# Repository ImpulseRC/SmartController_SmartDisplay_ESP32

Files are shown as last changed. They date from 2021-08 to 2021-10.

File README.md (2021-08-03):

# [ SmartController & SmartDisplay ]
⚠️ **Warning : this is work in progress. I decline all responsability about using informations from this project** ⚠️

To contribute and help this project :

 

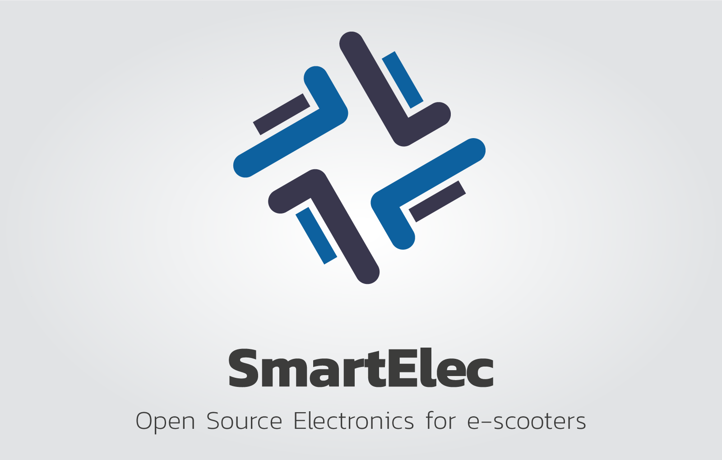
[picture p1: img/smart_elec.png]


## What is SmartController ?
It's a combo of electronic and smartphone application. It extend all features from original Minimotors EYE LCD and Minimotors controller, but it can also interface Zero, Apollo, Vsett, VESC adnd Kelly controllers.
The electronic board will interract with most of the e-scooter electronic when you plug it.
You simply place the little box inside the deck and connect it to the controller (and other electric parts if you want more features)

## What is SmartDisplay ?
It is an extension of the SmartController to completly replace the standard display of the escooter.
It mainly uses the same hardware/software.
For hardware, you only need to add a small extension board with the correct FPC connector... and of course, the LCD screen.

Render_night

## Requirements
- An e-scooter with any supported controllers (single or dual)
- An power supply between 36V and 100V... (possible with external DC-DC providing 5V if needed)
- If you want to use progressive brake feature, you must ensure no more than 60V pass in the brake handle (issue noted only for Kaabo)
- The electronics (ESP32 Dev KitC V4 + SmartController shield + JST SM/PH connectors + SmartDisplay shield if you want to connect the LCD display)
- Some electronic skills

## Features
| **Features** | **SmartController** | **SmartDisplay** | **Note** |
|:---|:---:|:---:|:---|
| Waterproof display with 3.5" screen | | ✅ | Need a custom lcd enclosure with handlebar bracket. |
| Progressive electric brake | ✅ | ✅ | |
| Temporary disable electric brake on high voltage | ✅ | ✅ | |
| Bluetooth android application with dashboard and settings | ✅ | ✅ | |
| Bluetooth and Wifi security integrated | ✅ | ✅ | BLE Encryption, Wifi WPA, HTTPS OTA |
| Wifi web application with dashboard and settings | ✅ | ✅ | |
| Intelligent battery autonomy computing with LG MJ1 cell reference | ✅ | ✅ | |
| Anti-theft with bluetooth proximity and manual locking | ✅ | ✅ | Up to 2 Bluetooth devices can be registered and scanned |
| Fast mode, acceleration, eco switches with smartphone | ✅ | ✅ | |
| Fast mode, acceleration, eco switches with custom hardware remote | ✅ | ✅ | Need a custom buttons enclosure with handlebar bracket. |
| Automatic shutdown after inactivity | ✅ | ✅ | |
| Custom acceleration curves | ✅ | ✅ | |
| Configurable speed limiter with fast on/off | ✅ | ✅ | |
| Multiple monitoring option like temperature, humidity, current/power | ✅ | ✅ | With SmartDisplay, it needs external sensors. |
| Push to start mode (PAS) | ✅ | ✅ | |
| Compatibility with Dualtron, Speedway, Futecher, Zero, Vsett, VESCs | ✅ | ✅ | VSett needs confirmation but it seems to be the same as Zero. Dual VESC needs work. |
| Over the air update with wifi connection | ✅ | ✅ | |
| Data logging on smartphone | ✅ | ✅ | |

## What can be done ?
I suggest you to have a look at all planed/added features in the image below.
There is almost no limit in custom features.
The controller power cannot exceed the nominal power, but with a shunt, you can increase the acceleration and still have a current control loop to limit the current by software (and avoid burning the controller).

Most settings will be configurable by the smartphone, and additionnal hardware buttons will allow you to control specific features.

Some examples : 
- It can lock the escooter with bluetooth proximity (with a beacon, the smartphone or any bluetooth device). When locked, the power is so reduced that nobody can ride it is you aren't close enouth. You can also manually lock the scooter with the Smartphone.

- You find the acceleration trigger to agressive at low speed ? you can change the acceleration curve for smooth trigger at low speed, and still have the beast once you push the trigger harder

- You want a mode for some weather conditions like 'rainy' with less torque ? no problem. Use fast settings access on the application dashboard or configuration hardware buttons.

- You feel the electric brake too strong at full power ? The progressive electric braking adjust the brake power with digital, or better, analog brake lever pressure sensor in real time.

- You can to limit speed to legal limits at startup ? Simply enable the option, and the speed limit can be removed with a brake pressure at startup or the smartphone.

- You want to control all settings for the Smartphone ? Use the Android native application or you can connect any device to the SmartElec in Wifi

- You want to know if there is not issue inside you escooter deck ? Temperature and humidity sensors will tell you is water entered inside the deck or if the ESC/battery is overheating.

**>>> [Check all detailed features here](/documents/FEATURES.md) <<<**

## Board assembly (v1.4.2)
Ass1

Ass2

Ass3

## Wrapping & Size
Current PCB size : 6.5cm (7cm with display connector) x 3.0cm x 1.5cm

Idea

## Electronic
### Compatibility
The software is designed for [ESP32 Dev Kit v4](https://docs.espressif.com/projects/esp-idf/en/latest/esp32/hw-reference/esp32/get-started-devkitc.html) microcontroller.

### Schematics
[PCB schematic v1.4.2](https://oshwlab.com/Koxx3/smartlcd-v1-4_copy)

[old - PCB schematic v1.3.2](https://oshwlab.com/Koxx3/smartlcd-v1-3_copy_copy)

PCB from easyEDA

PCB from easyEDA

### Protype parts list
[Google sheet](https://docs.google.com/spreadsheets/d/11n0oXzwr5ERSipWXZO53-mBwc6KPEdF8Q-aYTcDPNbk/edit?usp=sharing)

### Inspiration to understand controller electronic
[China BLDC motor controller 36v 250W](http://avdweb.nl/Article_files/Solarbike/Motor-controller/China-BLDC-motor-controller-36V-250W.pdf)

## 3D parts
<p float="left">
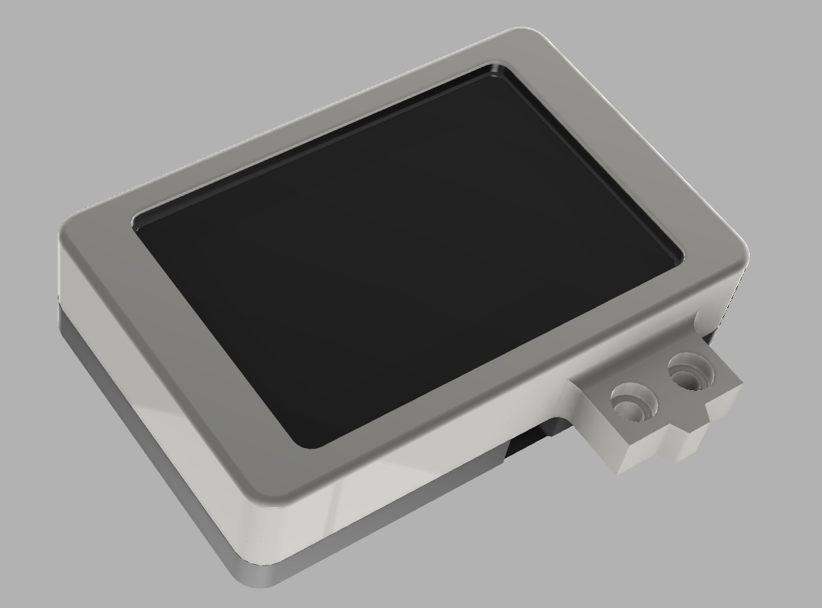
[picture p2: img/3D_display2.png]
  
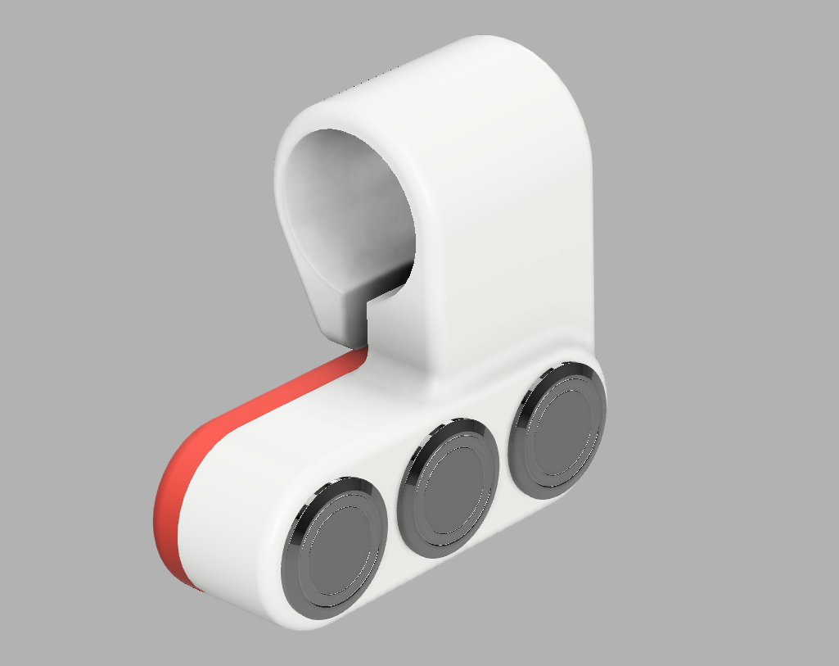
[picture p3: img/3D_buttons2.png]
   
</p>

The display and buttons cases are available here : [STL Parts](/stl/)

## Applications
### Android 
[SmartElec Application - Google play](https://play.google.com/store/apps/details?id=org.koxx.smartcntrl)

### iPhone
I have no skills in iPhone apps. If anyone wants to develop, let me know 😉

## ToDo / Done

- Escooter controllers ↔️
  - [✅] Serial Minimotors
    - [✅] Read/write serial link LCD_TO_CNTRL
    - [✅] Read/write serial link CNTRL_TO_LCD
    - [✅] Decode speed/mode/brake/regulator from serial link
    - [✅] Frame error detection
    - [IN PROGRESS 🔄] Error codes processing
      - [✅] Controller under voltage error
      - [✅] Throttle voltage
      - [✅] Brake voltage
      - [ ] Controller other error
  - [✅] VESC
    - [✅] Read serial link
    - [✅] Decode datas : speed, voltage, current
    - [✅] Set speed 1/2/3 modes
    - [✅] Electric brake max power setting
    - [✅] PAS
    - [✅] Lock (anti-theft or manual)
    - [✅] Speed computing
    - [✅] Temperature feedback
    - [✅] Brake power smartphone feedback
    - [✅] Speed limiter
    - [✅] Power processing / display
    - [✅] Brake forbiden on high voltage
    - [✅] Electric analog brake processing
    - [✅] Electric digital brake processing
    - [IN PROGRESS 🔄] Dual VESC - **PRO Version**
      - [ ] Change speed limits
      - [ ] Change current/acceleration limits
      - [ ] Get infos
    - [ ] Error codes processing
      - [ ] Temperature alarm
      - [ ] Other errors
  - [✅] Zero/Apollo
    - [✅] Read serial link
    - [✅] Decode datas : speed, mode, power, pas ...
    - [✅] Set speed 1/2/3 modes
    - [✅] Speed computing
    - [✅] Speed limiter
    - [✅] Lock (anti-theft or manual)
    - [✅] PAS
    - [✅] Set accel mode
    - [✅] Electric brake max power setting
    - [✅] Brake power smartphone feedback
    - [✅] Brake forbiden on high voltage
    - [✅] Electric analog brake processing
    - [✅] Electric digital brake processing
    - [ ] Error codes processing
  - [✅] Kelly
    - [✅] Read serial link
    - [✅] Decode datas : speed, voltage, controller temperature
    - [ ] Error codes processing

- Communications
  - [✅] Bluetooth 
    - [✅] Communication with Android
    - [✅] Dashboard
    - [✅] Anti-theth with smartphone
    - [✅] Anti-theth with beacon (scan & rssi detection)
    - [✅] Lock beacon or device settings
    - [✅] SmartController connection security (PIN code)
    - [✅] SmartController connection with multi devices (BT device choice)
    - [✅] Settings
    - [✅] Flash firmware
  - [✅] Wifi
    - [✅] Settings
    - [✅] Flash firmware
    - [IN PROGRESS 🔄] Dashboard

- Other inputs/outputs ↔️
    - [✅] Read current with WCS1700
    - [✅] Read battery voltage
    - [✅] Read tempertature/humidity with DHT11/DHT22
    - [✅] Read break handle position on serial
    - [✅] Read break handle position on standard brake handle
    - [✅] Read break handle position on analog brake handle
    - [✅] Read buttons
    - [✅] Send break handle position to controller
    - [✅] Send LED status
    - [✅] Send optocopler order
    - [✅] Internal temperature sensor
    - [✅] Throttle signal regeneration
    - [IN PROGRESS 🔄] External expansion boards - **PRO Version**
      - [✅] IO and sensors
      - [IN PROGRESS 🔄] GPS & anti-theft
      - [IN PROGRESS 🔄] Time and date 

- Power 🔋
    - [✅] Convert 12V to 5V
    - [✅] Convert 80V to 5V
    - [✅] Convert 100V to 5V

- Features ⚙️
  - [✅] Save settings in non volatile memory
  - [✅] Progressive electric braking (software detection)
  - [✅] Progressive electric braking (hardware analog detection)
  - [✅] OTA update
  - [✅] Current measure auto calibration (at startup)
  - [✅] Current measure manual calibration
  - [✅] Speed limiter at startup
  - [✅] Configurable speed limit
  - [✅] Remote physical button
    - [✅] Speed limiter ON/OFF
    - [✅] Lock ON      
    - [✅] Nitro Boost continuous
    - [✅] Nitro Boost ON/OFF
    - [✅] Aux ON/OFF       
    - [✅] Switch modes 1/2/3 or 2/3   
    - [✅] Settings access
  - [✅] Disable electric brake with full battery
  - [✅] Manual calibration for analog brake
  - [✅] Manual calibration for voltage
  - [✅] Use brake switch as startup for speed limiter
  - [✅] LCD Speed adjustment
  - [✅] Exponential acceleration curve
  - [✅] PAS switch
  - [✅] Custom acceleration curves (linear/expo/custom)
  - [✅] Automatic power off
  - [IN PROGRESS 🔄] Dynamic BLE debug infos

- Android application 📱
  - [✅] Display : 
    - [✅] Speed
    - [✅] Mode
    - [✅] Voltage
    - [✅] Current
    - [✅] Power
    - [✅] Brake mode (PA)
    - [✅] Max speed
    - [✅] Max power
    - [✅] Max current
    - [✅] Temperature
    - [✅] Humidity
    - [✅] Time
    - [✅] Moving time
    - [✅] Odometer / distance
    - [✅] Trip distance
    - [✅] Average speed
    - [✅] Autonomy
    - [✅] Brake forbiden
    - [✅] Errors
  - [✅] Auto-launch app with NFC tag
  - [✅] Parameters custom settings
  - [✅] Data logging
  - [✅] History graphics
  - [✅] Integrated settings help
  - [IN PROGRESS 🔄] Wizzard for calibrations
   
- iPhone application 🍏
  - use wifi dashboard

## Let's go ! :kick_scooter:

- [Escooter wiring diagrams](https://oshwlab.com/Koxx3/smartelec_wiring)
- [Produce your own board](/documents/MAKE_IT.md)
- [Wiring](/documents/WIRING.md)
- [Run it !](/documents/RUN.md)
- [Settings description](/documents/help_settings_en.md)

## Ressources 🔗
- [Serial links data decoding - Excel XLSX](/documents/MINIMO.xlsx)

## Hardware revisions  :stopwatch:
**1.4.2**
- fix throttle ADC voltage for external throttle
- add LCD display backlight control
- switch to LM5164 regulator
- add power latch

## Donate to support :moneybag:
[If you want to support me, click here !](https://paypal.me/koxx3/)

## License
[The code is under GNU GPL v3 license](/LICENSE)
All code usage must be redistributed in public.

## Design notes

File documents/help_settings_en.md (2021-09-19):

# Settings manual

## Escooter characteristics
### Wheel size
Valid configuration : SmartController / SmartDisplay<br>
Default value : 10.0 (inches)<br>
<br>
Usage : Wheel size (in inches) is used to adjust the speed and distance when riding.<br>
                
### Number of poles pairs
Valid configuration : SmartController / SmartDisplay<br>
Default value : 15<br>
<br>
Usage : Motors number of poles are used to compute speed/distance. Check you manual to set the correct value. If the manual specify '30 poles', set 15.<br>
                
### Battery nominal voltage
Valid configuration : SmartController / SmartDisplay<br>
Possible values : <br>
    - 36V (42V full / 10S) (value = 0)<br>
    - 48V (54,6V full / 13S) (value = 1)<br>
    - 52V (58,8V full / 14S) (value = 2)<br>
    - 60V (67,2V full / 16S) (value = 3)<br>
    - 72V (84V full / 20S) (value = 4)<br>
    - 86V (100,8V full / 24S) (value = 5)<br>
Default value : 2<br>
<br>
Usage : Battery voltage is used to compute the autonomy left and charge indicator. Check your manuel or charger (it indicate full charge voltage) to set the correct setting.<br>
                
### Battery maximum distance
Valid configuration : SmartController / SmartDisplay<br>
Default value : 40 (kilometers)<br>
<br>
Usage : Used to compute autonomy. Set your regular max distance with one full charge.
Autonomy is computed following the LG MJ1 discharge curve.<br>

## General
### Speed limiter at startup
Valid configuration : SmartController / SmartDisplay<br>
Default value : 0<br>
<br>
Usage : Enable speed limit after power on. It set a power limit on most escooters (Dualtron/Speedway/Zero …) or real speed limit on VESC.
For Dualtron/Speedway/Zero, you need to find the right setting if you want to limit it to the legal speed limit.
Once enabled, it will limit the displayed speed to 25 km/h.<br>
                
### Speed limiter max speed
Valid configuration : SmartController / SmartDisplay<br>
Default value : 37<br>
<br>
Usage : Power limit is expressed in percent (same power setting as in your manual). For VESC, the speed limit is set to 25 Km/h.<br>
                
### Bluetooth lock mode
Valid configuration : SmartController / SmartDisplay<br>
Possible values : <br>
    - None (value = 0)<br>
    - Smartphone connected (value = 1)<br>
    - Smartphone connected or beacon visible (value = 2)<br>
    - Beacon visible (value = 3)<br>
Default value : 0<br>
<br>
Usage : Lock the scooter if bluetooth device check is not successful :
- None : no bluetooth peripheral check, no lock mecanism.
- Smartphone connected : your smartphone needs to be connected to the SmartElec device in Bluetooth to unlock the scooter.
- Smartphone connected or beacon visible : your smartphone needs to be connected OR a BLE (Bluetooth Low Energy) must be in range beacon of the SmartElec device in Bluetooth to unlock the scooter.
- Beacon visible : BLE beacon must be in range of the SmartElec device in Bluetooth to unlock the scooter.
<b>Those modes are used as anti-theft protection</b>. If an thief try to still you escooter, as soon as the escooter is out of range of your bluetooth device, it will cut power of the escooter.<br>
                
### PIN code
Valid configuration : SmartController / SmartDisplay<br>
Default value : 147258<br>
<br>
Usage : Bluetooth PIN code is used when you want to connect a smartphone to your SmartElec device. <b>Change it to protect your SmartElec device from any anybody connection.</b><br>
                
### Beacon Mac Address 1
Valid configuration : SmartController / SmartDisplay<br>
Default value : aa:bb:cc:dd:ee:ff<br>
<br>
Usage : To search a beacon you must specify the beacon mac address. 
Search on your smartphone store for a 'BLE Scanner', it will scan all Bluetooth devices and the MAC address (an unique identifier) for the beacon, then enter this MAC address in this setting.<br>
You can use any Bluetooth Low Energy device as beacon (any BLE band/bracelet for example) or use a BLE beacon (10$ on aliexpress).
Important : you cannot search for most smartphone because they are protected against search scan.<br>
                
### Beacon Mac Address 2
Valid configuration : SmartController / SmartDisplay<br>
Default value : aa:bb:cc:dd:ee:ff<br>
<br>
Usage : Same as 'Beacon Mac Address 1' but for a second device. If one is found in range, the escooter is unlocked.<br>
                
### Smartphone or Beacon Mac range
Valid configuration : SmartController / SmartDisplay<br>
Default value : -80 (dB)<br>
<br>
Usage : Minimal reception power of the beacon to unlock the escooter. This is in dB, it means a -100dB value will be a longer distance than -50dB.<br>
                
### Original display speed adjustment (in percent)
Valid configuration : SmartController / SmartDisplay<br>
Default value : 0 (percent)<br>
<br>
Usage : Use this value to correct the speed on the escooter display.
You can increase or decrease the speed.
Set at -50%, it will display 25km/h when riding at 50km/h.<br>
                
### Temperature warning
Valid configuration : SmartController / SmartDisplay<br>
Default value : 70 (celcuis)<br>
<br>
Usage : Trig an error indicator on the display or the smartphone application if this temperature threshold is reached. If you place the temperature sensor inside the deck, it will warn you if the controller or the battery are too hot.<br>
                
### Humidity warning
Valid configuration : SmartController / SmartDisplay<br>
Default value : 80 (RH)<br>
<br>
Usage : Trig an error indicator on the display or the smartphone application if this humidy threshold is reached. If you place the humidity sensor inside the deck, it will warn you if the water is entered inside the deck.<br>
                
### Automatic power off
Valid configuration : SmartDisplay<br>
Possible values : <br>
    - None (value = 0)<br>
    - 2 min (value = 1)<br>
    - 3 min (value = 2)<br>
    - 4 min (value = 3)<br>
    - 5 min (value = 4)<br>
    - 10 min (value = 5)<br>
    - 15 min (value = 6)<br>
    - 20 min (value = 7)<br>
    - 30 min (value = 8)<br>
    - 60 min (value = 9)<br>
Default value : 0<br>
<br>
Usage : Automatically shutdown the escooter after this period when escooter is not moving.<br>

## Smartphone display
### Speed adjustment (in percent)
Valid configuration : SmartController / SmartDisplay<br>
Default value : 0<br>
<br>
Usage : Use this value to correct the speed on the smartphone display.
You can increase or decrease the speed.<br>
                
### Aux relay name
Valid configuration : SmartController / SmartDisplay<br>
Possible values : <br>
    - AUX (value = 0)<br>
    - DUAL (value = 1)<br>
    - LIGHT (value = 2)<br>
    - HORN (value = 3)<br>
    - RELAY (value = 4)<br>
Default value : 0<br>
<br>
Usage : Change the name of the auxilary relay on the display and smartphone for the integrated relay action. Exemple : if you connect a light, you can display "light" on the dashboard instead of "aux".<br>
                
### Display GPS speed instead of escooter speed
Valid configuration : SmartController / SmartDisplay<br>
Default value : 0<br>
<br>
Usage : Display GPS speed instead of escooter speed on the smartphone display.<br>

## SmartDisplay
### Default mode at startup
Valid configuration : SmartDisplay<br>
Default value : 3<br>
<br>
Usage : Default speed mode after escooter power up.<br>
                
### Default eco mode at startup
Valid configuration : SmartDisplay<br>
Possible values : <br>
    - Max (value = 0)<br>
    - Medium (value = 1)<br>
    - None (value = 2)<br>
Default value : 2<br>
<br>
Usage : Default eco mode after escooter power up.<br>
                
### Default acceleration
Valid configuration : SmartDisplay<br>
Possible values : <br>
    - Maximum (value = 0)<br>
    - Very fast (value = 1)<br>
    - Fast (value = 2)<br>
    - Medium (value = 3)<br>
    - Slow (value = 4)<br>
    - Very slow (value = 5)<br>
Default value : 0<br>
<br>
Usage : Default acceleration mode after escooter power up.<br>
                
### Default electric brake at startup
Valid configuration : SmartDisplay<br>
Default value : 3<br>
<br>
Usage : Default electric brake power mode after escooter power up.<br>
                
### PAS enabled
Valid configuration : SmartDisplay<br>
Default value : 0<br>
<br>
Usage : The 'pedal assitance switch' will force you to push the escooter to start the engine. 
If you don't push the scooter, the throttle is not effective. The motor will engage as soon as 1km/h is reached.<br>
                
### ABS enabled
Valid configuration : SmartDisplay<br>
Default value : 0<br>
<br>
Usage : Enable the anti-lock electric braking system (not advised, not well implemented on most escooters),<br>
                
### Display brightness
Valid configuration : SmartDisplay<br>
Default value : 100<br>
<br>
Usage : Set the SmartDisplay screen brightness.<br>
                
### Display splash screen
Valid configuration : SmartDisplay<br>
Default value : 1<br>
<br>
Usage : Enable the splash screen at escotter startup<br>
                
### Rotate screen
Valid configuration : SmartDisplay<br>
Possible values : <br>
    - Normal (value = 0)<br>
    - Inverted (value = 1)<br>
Default value : 0<br>
<br>
Usage : Rotate screen if you mount the display in un unorthodox way.<br>

## Electric brake
### Progressive mode
Valid configuration : SmartController / SmartDisplay<br>
Default value : 0<br>
<br>
Usage : Enable the electric brake progressive mode.<br>
                
### Smart brake type
Valid configuration : SmartController / SmartDisplay<br>
Possible values : <br>
    - Controller (value = 0)<br>
    - Smart - Digital brake lever (value = 1)<br>
    - Smart - Analog brake lever (value = 2)<br>
    - Smart - Digital brake + throttle (exp) (value = 3)<br>
Default value : 0<br>
<br>
Usage : If you enable the electric progressive mode, the braking feedback must arrive to the SmartElec device. <b>There is mulitple possibilities to wire the brake on the SmartElec and you MUST select the brake type according to your wiring</b> :
- Controller : no specific wiring required, the brake feedback will come from the controller. This is slower and will add a delay of 200/300ms between the brake pressure and the electric brake activation. The brake force will be determined by the brake lever pressure time. Longer you press, stronger the electric brake will become.
- Smart - Digital brake lever : a standard on/off brake lever is wired directly to the SmartElec device. This wiring has a faster reaction. The brake force will be determined by the brake lever pressure time. Longer you press, stronger the electric brake will become.
- Smart - Analog brake lever : an analog brake lever (xiaomi type or any hall sensor brake lever) is wired to directly to the SmartElec device. This wiring is the best. The brake force will be determined by the brake lever pressure force.
- Smart - Digital brake + throttle (experimental) : a standard on/off brake lever is wired directly to the SmartElec device and the throttle pressure set the brake force. You will need time to use this mode when riding.<br>
                
### Input min voltage (in millivolts)
Valid configuration : SmartController / SmartDisplay<br>
Default value : 650 (millivolts)<br>
<br>
Usage : Throttle input signal voltage when the throttle is released.
Note : if the motor is spinning when the throttle is not pressed, try to decrease this value.<br>
                
### Input max voltage (in millivolts)
Valid configuration : SmartController / SmartDisplay<br>
Default value : 3950 (millivolts)<br>
<br>
Usage : Throttle input signal voltage when the throttle is fully pressed
Note : if the motor is not reaching max speed when the throttle is pressed, try to increase this value.<br>
                
### Min power value
Valid configuration : SmartController / SmartDisplay<br>
Default value : 1<br>
<br>
Usage : Define the minimum electric brake force when you start pressing the brake lever.
Note : don't forget to calibrate the brake lever pressure for a better feeling.<br>
                
### Max power value
Valid configuration : SmartController / SmartDisplay<br>
Default value : 5<br>
<br>
Usage : Define the maximum electric brake force when you pressing the brake lever.
Note : don't forget to calibrate the brake lever pressure for a better feeling.<br>
                
### Time between mode shift
Valid configuration : SmartController / SmartDisplay<br>
Default value : 500 (milliseconds)<br>
<br>
Usage : When using a digital brake lever (on/off switch on the lever), this period will determine when the brake force is increased to the next lever (from min to max) as long as you keep the brake active.
Exemple : brake min = 1 / brake max = 3 / brake switch period = 500ms. When you start pressing the brake, it will set a electric brake force at 1. If you keep the brake pressed, 500ms later, it will set a electric brake force at 2, and 500ms later to 3. It will remain at 3 (max) until you release the brake lever.<br>
                
### Disabled on high battery voltage
Valid configuration : SmartController / SmartDisplay<br>
Default value : 0<br>
<br>
Usage : Prevent power surge when braking if the battery is full or almost full. 
Electric brake generate current/voltage when used. If you use the electric brake when the battery is battery is full, the battery cannot take the energy and the controller will try to dissipate the energy... and can heat/blow.
This option disable the electric brake until the baterry reach a threshold.<br>
                
### Disabled percent limit
Valid configuration : SmartController / SmartDisplay<br>
Default value : 100 (percent)<br>
<br>
Usage : Battery load percent threshold to reach to enable electric brake.<br>

## Throttle
### Throttle regeneration
Valid configuration : SmartController / SmartDisplay<br>
Default value : 0<br>
<br>
Usage : Enable throttle signal regeneration.
This option allow you to modify the acceleration curve to make it more/less dynamic with different acceleration curves.
<b>To enable this feature, you must wire the trottle jumpers according to the WIRING documentation.</b><br>
                
### Input min voltage (in millivolts)
Valid configuration : SmartController / SmartDisplay<br>
Default value : 650 (millivolts)<br>
<br>
Usage : Throttle input signal voltage when the throttle is released.
Note : if the motor is spinning when the throttle is not pressed, try to decrease this value.<br>
                
### Input max voltage (in millivolts)
Valid configuration : SmartController / SmartDisplay<br>
Default value : 3950 (millivolts)<br>
<br>
Usage : Throttle input signal voltage when the throttle is fully pressed
Note : if the motor is not reaching max speed when the throttle is pressed, try to increase this value.<br>
                
### Output min voltage (in millivolts)
Valid configuration : SmartController / SmartDisplay<br>
Default value : 800 (millivolts)<br>
<br>
Usage : Throttle ouput signal voltage when the throttle is released.
Note : if the motor is spinning when the throttle is not pressed, try to decrease this value.<br>
                
### Output max voltage (in millivolts)
Valid configuration : SmartController / SmartDisplay<br>
Default value : 3350 (millivolts)<br>
<br>
Usage : Throttle output signal voltage when the throttle is fully pressed
Note : if the motor is not reaching max speed when the throttle is pressed, try to increase this value.<br>
                
### Output curve
Valid configuration : SmartController / SmartDisplay<br>
Possible values : <br>
    - Linear (value = 0)<br>
    - Exponential 1 (value = 1)<br>
    - Exponential 2 (value = 2)<br>
    - Exponential 3 (value = 3)<br>
    - Exponential 4 (value = 4)<br>
    - Custom 6 points (value = 5)<br>
Default value : 2<br>
<br>
Usage : This option modify the throttle response and acceleration curve.
There is 3 main modes :
- linear : same as original, except you can put  an offset to increase the dead zone (with min input voltage)
- exponential : those curves follow exponential functions, the acceleration becomes more violent as you reach the end the trigger pressure. Exponential 1 is soft but more violent than linear, Exponential 4 is very violent.
- custom 6 points : 2 points are fixed (0% trigger pressure = 0% output / 100% trigger pressure = 100% output), with the next option, you can the set the output percent for 20, 40, 60 and 80% pressure on the trigger. It will interpolate the values between those pressure percentage to determine the ouput throttle percentage.<br>
                
### Custom output curve points
Valid configuration : SmartController / SmartDisplay<br>
Default value : 20,40,60,80<br>
<br>
Usage : String of 4 values separated by commas.
It will determine the output level for the 4 points (see custom curve option above) of 20, 40, 60, 80% pressure.
Example with : 7, 15, 45, 75
<br>

## Escooter buttons
### Button 1 short press action
Valid configuration : SmartController / SmartDisplay<br>
Possible values : <br>
    - None (value = 0)<br>
    - Speed limit ON/OFF (value = 1)<br>
    - Aux ON/OFF (value = 2)<br>
    - Mode switch 1/2/3 (value = 3)<br>
    - Mode switch 2/3 (value = 4)<br>
    - Eco switch NONE/MED/MAX (value = 5)<br>
    - Eco switch NONE/MED (value = 6)<br>
Default value : 0<br>
<br>
Usage : Set the button 1 short press action (for external buttons wired to the SmartElec) :
- None : no action
- Speed limitation ON/OFF : enable/disable the speed limiter
- Aux ON/OFF : enable/disable the auxiliary relay output
- Mode switch 1/2/3 : switch between speed modes
- Mode switch 2/3 : switch between speed modes
- Eco switch NONE/MED/MAX : switch between eco modes
- Eco switch NONE/MED : switch between eco modes
- Anti-theft manual lock ON : lock the escooter (motor power is locked, nobody can steal & ride with this mode)
- Nitro boost continuous : switch speed mode to 3 while the button is pressed, then go back to original speed mode<br>
                
### Button 1 long press action
Valid configuration : SmartController / SmartDisplay<br>
Possible values : <br>
    - None (value = 0)<br>
    - Speed limitation ON/OFF (value = 1)<br>
    - Aux ON/OFF (value = 2)<br>
    - Mode switch 1/2/3 (value = 3)<br>
    - Mode switch 2/3 (value = 4)<br>
    - Eco switch NONE/MED/MAX (value = 5)<br>
    - Eco switch NONE/MED (value = 6)<br>
    - Anti-theft manual lock ON (value = 7)<br>
    - Nitro boost continuous (value = 8)<br>
Default value : 0<br>
<br>
Usage : Set the button 1 long press action (for external buttons wired to the SmartElec) :
- None : no action
- Speed limitation ON/OFF : enable/disable the speed limiter
- Aux ON/OFF : enable/disable the auxiliary relay output
- Mode switch 1/2/3 : switch between speed modes
- Mode switch 2/3 : switch between speed modes
- Eco switch NONE/MED/MAX : switch between eco modes
- Eco switch NONE/MED : switch between eco modes
- Anti-theft manual lock ON : lock the escooter (motor power is locked, nobody can steal & ride with this mode)
- Nitro boost continuous : switch speed mode to 3 while the button is pressed, then go back to original speed mode<br>
                
### Button 2 short press action
Valid configuration : SmartController / SmartDisplay<br>
Possible values : <br>
    - None (value = 0)<br>
    - Speed limitation ON/OFF (value = 1)<br>
    - Aux ON/OFF (value = 2)<br>
    - Mode switch 1/2/3 (value = 3)<br>
    - Mode switch 2/3 (value = 4)<br>
    - Eco switch NONE/MED/MAX (value = 5)<br>
    - Eco switch NONE/MED (value = 6)<br>
Default value : 0<br>
<br>
Usage : Set the button 2 short press action (for external buttons wired to the SmartElec) :
- None : no action
- Speed limitation ON/OFF : enable/disable the speed limiter
- Aux ON/OFF : enable/disable the auxiliary relay output
- Mode switch 1/2/3 : switch between speed modes
- Mode switch 2/3 : switch between speed modes
- Eco switch NONE/MED/MAX : switch between eco modes
- Eco switch NONE/MED : switch between eco modes
- Anti-theft manual lock ON : lock the escooter (motor power is locked, nobody can steal & ride with this mode)
- Nitro boost continuous : switch speed mode to 3 while the button is pressed, then go back to original speed mode
Note : button 2 long press action allow you to enter the settings menu.<br>
                
### Button long press duration
Valid configuration : SmartController / SmartDisplay<br>
Default value : 3 (seconds)<br>
<br>
Usage : If you press the button for this period, the SmartElec will launch the "long press" action.<br>

## OTA update
### Wifi network name (SSID)
Valid configuration : SmartController / SmartDisplay<br>
Default value : <br>
<br>
Usage : Wifi network SSID/name used for software updates.<br>
                
### Wifi password
Valid configuration : SmartController / SmartDisplay<br>
Default value : <br>
<br>
Usage : Wifi network password used for software updates.<br>

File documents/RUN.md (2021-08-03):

# Run the softwares
Once you have all the electronic, you'll need to flash/install the softwares.

- First : the ESP32 software
- Second : the Android application (search 'SmartElec" on Google Play)

## Versions

Firmwares are labeled as follow : `smart<xxx>_<yyyy>[_<zzzz>]`
- xxx : smartcontroller = without screen / smartdisplay = with screen
- yyy : escooter controller type
- zzz : screen type (2.4 = ILI9341 / 3.5 = ILI9481 / 3.5v3 = ST7796)
  
## Preparation of ESP32 board
- Install Visual Code + Platform.io [tuto](https://platformio.org/install/ide?install=vscode)
- Clone this Github project
- Patch Espressif Framework with patch folder in :
  - copy patch-esp\esp32-hal-uart.* in C:\Users\ \<username>\ \.platformio\packages\framework-arduinoespressif32\cores\esp32
  - copy patch-esp\HardwareSerial.* in C:\Users\ \<username>\ \.platformio\packages\framework-arduinoespressif32\cores\esp32
  - copy patch-esp\BLESecurity.* in C:\Users\ \<username>\ \.platformio\packages\framework-arduinoespressif32\libraries\BLE\src
- Burn efuse for GPIO12 with the script called 'burn_efuse_gpio12.bat'
  - burn_efuse_gpio12.bat <COM_PORT>
- Erase the ESP32
- Flash ESP32 application partition
- Flash ESP32 data partition

## Configure the device
### Android
- Enable bluetooth
- Check if bluetooth detect a "SmartContrl-xxxx" device
- Pair the device with the default PIN code
- Install the applcation from the Google App Store : https://play.google.com/store/apps/details?id=org.koxx.smartcntrl
- Launch the application
- Accept the connection to the device
- Use the defaul pin code : 147258
  - Nota : You can change the pin code in the application settings page
- Enter the applicationsettings page
- Configure the device

### iPhone
- Enable wifi
- Search for "SmartContrl-xxxx" wifi
- Connect to the SmartElec hotsport, enter the password 147258147258 (this is the Bluetooth PIN code repeated twice) and access the hotspot page
  - Nota : The password is the Bluetooth pin code repeated twice. Change the Bluetooth pin code to change the wifi password.
- Enter in the settings menu

### From the SmartDisplay
- Long press the secondary button, you will enter in the settings menu
 - Nota : some settings are not available from this menu (when you have to enter strings)
- Use primary and secondary buttons to move the cursor, validate and escape

## Settings
[See settings descriptions](help_settings_en.md)

## Update throught Wifi
You need to set the Wifi network/password from an android/iphone to make it work :
Then ...

### Android
- In the main interface, open the menu with the '...' , tap "Software update (OTA)"
=> The SmartController will switch from bluetooth to wifi server and you will loose Bluetooth connection.
- Wait the upload and flash end, then it should reboot automatically

### iPhone
- On the wifi hotspot portal, select "Software update (OTA)"
- Enter the release number and validate !

### From the SmartDisplay
- TBD

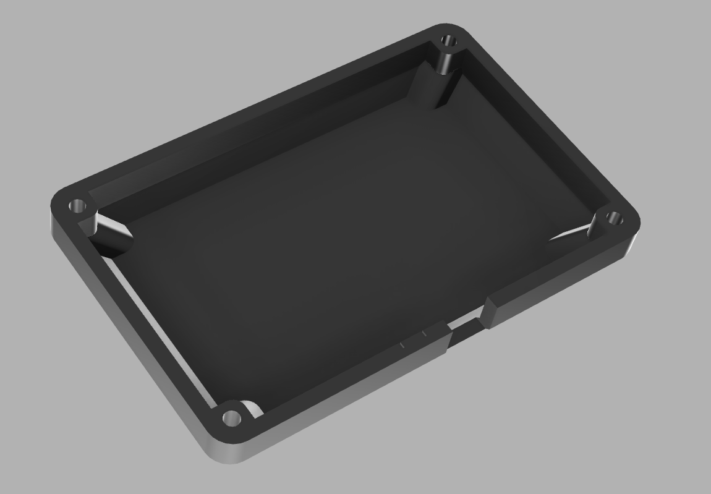
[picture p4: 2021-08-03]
img/3D_display5.png

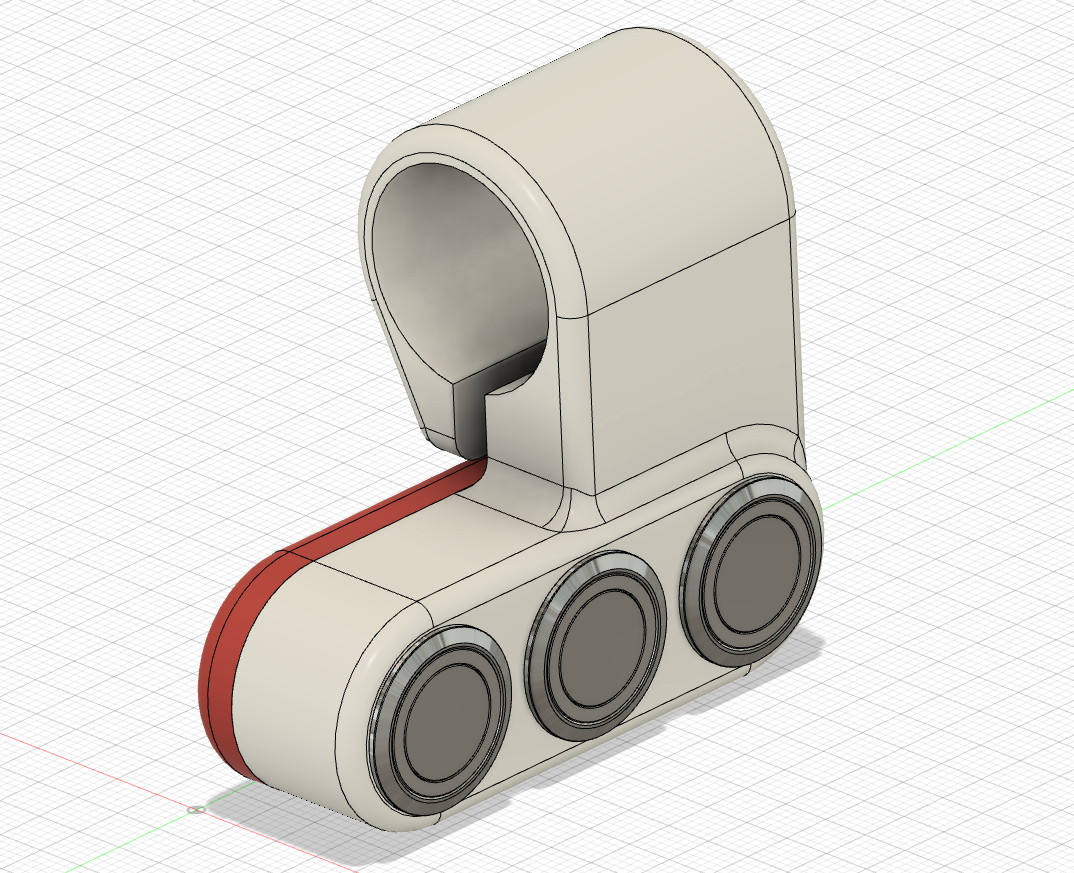
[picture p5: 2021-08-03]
img/3D_buttons1.png

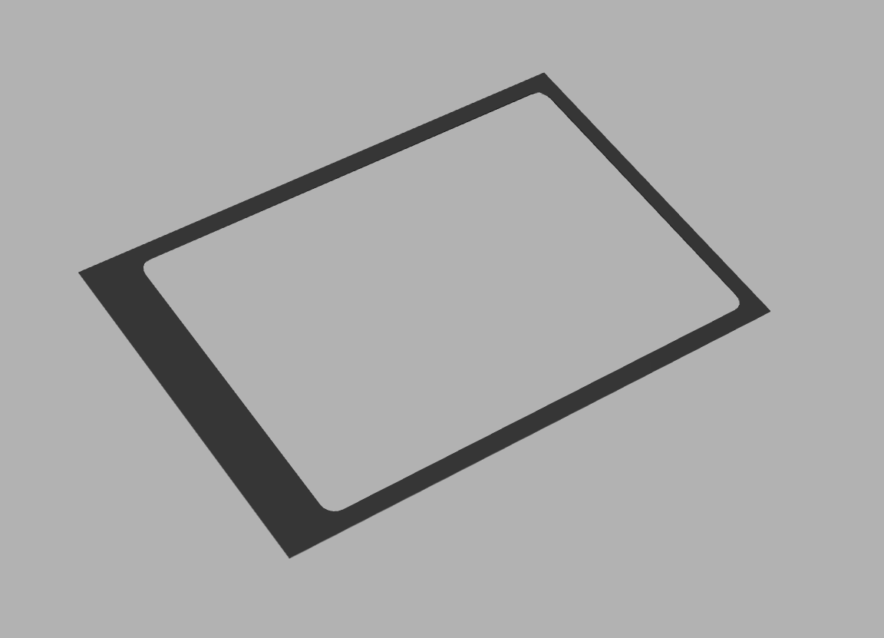
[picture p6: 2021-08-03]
img/3D_display4.png

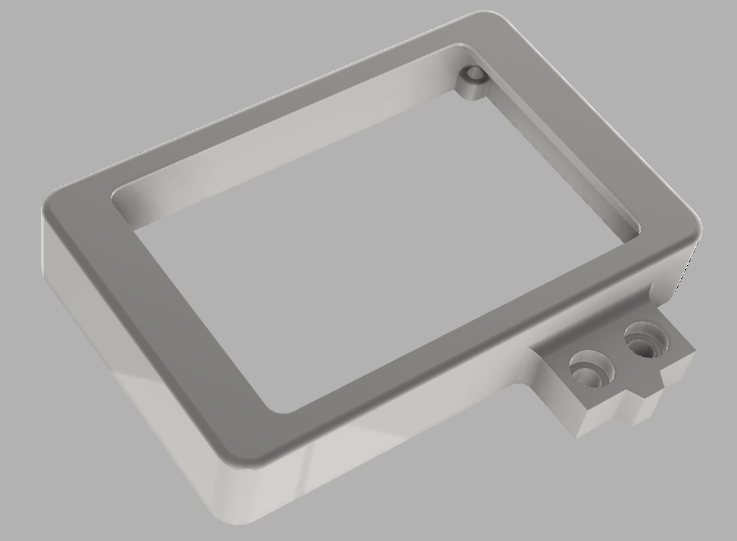
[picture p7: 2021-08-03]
img/3D_display3.png

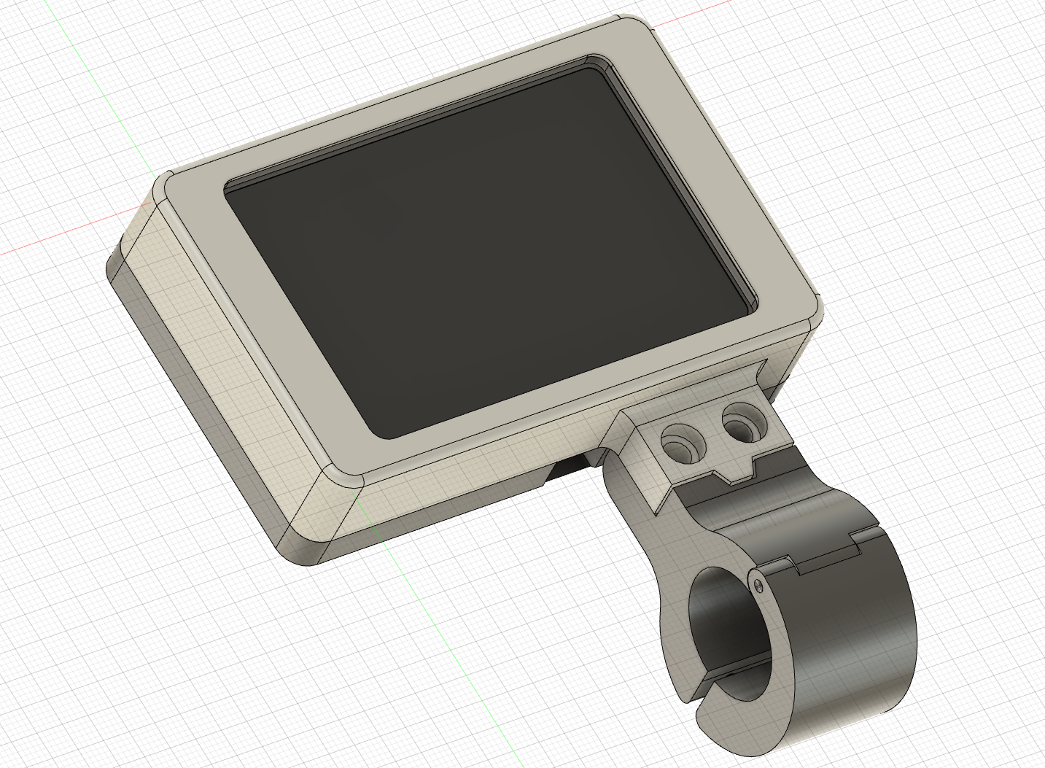
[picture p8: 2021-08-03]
img/3D_display1.png

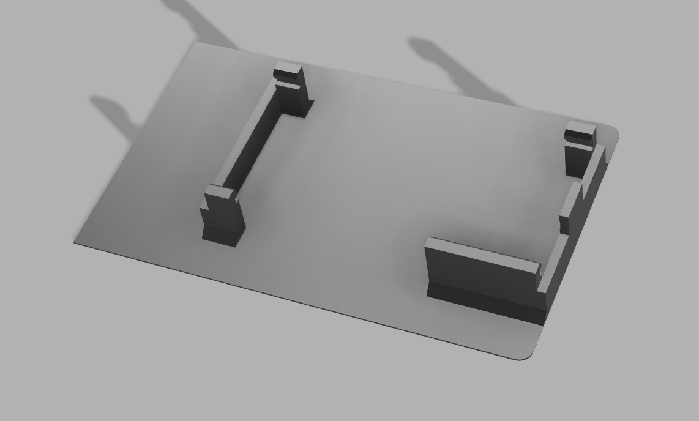
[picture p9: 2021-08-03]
img/3D_display6.png

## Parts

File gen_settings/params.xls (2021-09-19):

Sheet: Settings
ble_id | class | class_order | type | var_name | valid_config | list_strings | min | max | default | increment | regex_valid | smartphone_display_name | smartphone_display_unit | smartphone_display_hint | smartphone_display_type | tft_menu_visible | tft_display_name | tft_fast_increment | tft_slow_increment | tft_unit | help_en
1 | Escooter characteristics | 1 | float | Wheel_size |  |  | 8 | 20 | 10 |  | ^[0-9]+[.]?[0-9]*([eE][-+]?[0-9]+)?$ | Wheel size | inches |  | edit_text_number_float | 1 | Wheel size | 0.5 | 0.1 | inch | Wheel size (in inches) is used to adjust the speed and distance when riding.
2 | Escooter characteristics | 1 | uint8_t | Number_of_poles_pairs |  |  | 10 | 30 | 15 | 1 | ^[0-9]+$ | Number of poles pairs |  |  | seek_bar | 1 | Number of poles pairs | 1 | 1 |  | Motors number of poles are used to compute speed/distance. Check you manual to set the correct value. If the manual specify '30 poles', set 15.
48 | Escooter characteristics | 1 | uint8_t | Battery_nominal_voltage |  | 36V (42V full / 10S) 48V (54,6V full / 13S) 52V (58,8V full / 14S) 60V (67,2V full / 16S) 72V (84V full / 20S) 86V (100,8V full / 24S) | 0 | 5 | 2 |  |  | Battery nominal voltage |  |  | list | 1 | Battery nominal voltage | 1 | 1 | V | Battery voltage is used to compute the autonomy left and charge indicator. Check your manuel or charger (it indicate full charge voltage) to set the correct setting.
5 | Escooter characteristics | 1 | uint8_t | Battery_maximum_distance |  |  | 10 | 100 | 40 |  | ^[0-9]+$ | Battery maximum distance | kilometers |  | edit_text_number_integer | 1 | Battery maximum distance | 5 | 1 | Km | Used to compute autonomy. Set your regular max distance with one full charge. Autonomy is computed following the LG MJ1 discharge curve.
6 | General | 2 | uint8_t | Speed_limiter_at_startup |  |  | 0 | 1 | 0 |  |  | Speed limiter at startup |  |  | checkbox | 1 | Speed limiter at startup |  |  |  | Enable speed limit after power on. It set a power limit on most escooters (Dualtron/Speedway/Zero …) or real speed limit on VESC. For Dualtron/Speedway/Zero, you need to find the right setting if you want to limit it to the legal speed limit. Once enabled, it will limit the displayed speed to 25 km/h.
7 | General | 2 | uint8_t | Speed_limiter_max_speed |  |  | 5 | 100 | 37 | 1 |  | Speed limiter max speed |  |  | seek_bar | 1 | Speed limiter max speed | 5 | 1 | % | Power limit is expressed in percent (same power setting as in your manual). For VESC, the speed limit is set to 25 Km/h.
8 | General | 2 | uint8_t | Bluetooth_lock_mode |  | None Smartphone connected Smartphone connected or beacon visible Beacon visible | 0 | 3 | 0 |  |  | Bluetooth lock mode |  |  | list | 0 | Bluetooth lock mode |  |  |  | Lock the scooter if bluetooth device check is not successful : - None : no bluetooth peripheral check, no lock mecanism. - Smartphone connected : your smartphone needs to be connected to the SmartElec device in Bluetooth to unlock the scooter. - Smartphone connected or beacon visible : your smartphone needs to be connected OR a BLE (Bluetooth Low Energy) must be in range beacon of the SmartElec device in Bluetooth to unlock the scooter. - Beacon visible : BLE beacon must be in range of the SmartElec device in Bluetooth to unlock the scooter. <b>Those modes are used as anti-theft protection</b>. If an thief try to still you escooter, as soon as the escooter is out of range of your bluetooth device, it will cut power of the escooter.
9 | General | 2 | uint32_t | Ble_pin_code |  |  | 0 | 999999 | 147258 |  | ^[0-9]{6,6}$ | PIN code |  |  | edit_text_number_integer | 0 | PIN code |  |  |  | Bluetooth PIN code is used when you want to connect a smartphone to your SmartElec device. <b>Change it to protect your SmartElec device from any anybody connection.</b>
10 | General | 2 | string | Ble_beacon_mac_address1 |  |  | 18 | 18 | aa:bb:cc:dd:ee:ff |  | ^([0-9A-Fa-f]{2}[:-]){5}([0-9A-Fa-f]{2})$ | Beacon Mac Address 1 |  | MAC address | edit_text_string | 0 | Beacon Mac Address 1 |  |  |  | To search a beacon you must specify the beacon mac address. Search on your smartphone store for a 'BLE Scanner', it will scan all Bluetooth devices and the MAC address (an unique identifier) for the beacon, then enter this MAC address in this setting.<br> You can use any Bluetooth Low Energy device as beacon (any BLE band/bracelet for example) or use a BLE beacon (10$ on aliexpress). Important : you cannot search for most smartphone because they are protected against search scan.
49 | General | 2 | string | Ble_beacon_mac_address2 |  |  | 18 | 18 | aa:bb:cc:dd:ee:ff |  | ^([0-9A-Fa-f]{2}[:-]){5}([0-9A-Fa-f]{2})$ | Beacon Mac Address 2 |  | MAC address | edit_text_string | 0 | Beacon Mac Address 2 |  |  |  | Same as 'Beacon Mac Address 1' but for a second device. If one is found in range, the escooter is unlocked.
11 | General | 2 | int8_t | Ble_beacon_range |  |  | -100 | -30 | -80 | 5 |  | Smartphone or Beacon Mac range | dB |  | seek_bar | 0 | Beacon range | 5 | 1 | dB | Minimal reception power of the beacon to unlock the escooter. This is in dB, it means a -100dB value will be a longer distance than -50dB.
12 | General | 2 | int8_t | Original_display_speed_adjustment |  |  | -100 | 100 | 0 |  | ^[-]?[0-9]+$ | Original display speed adjustment (in percent) | percent | write -10 to decrease speed by 10% | edit_text_number_integer_signed | 1 | Speed adjustment | 5 | 1 | % | Use this value to correct the speed on the escooter display. You can increase or decrease the speed. Set at -50%, it will display 25km/h when riding at 50km/h.
13 | General | 2 | uint8_t | Temperature_warning |  |  | 50 | 100 | 70 | 10 |  | Temperature warning | celcuis |  | seek_bar | 1 | Temperature warning | 10 | 5 | °C | Trig an error indicator on the display or the smartphone application if this temperature threshold is reached. If you place the temperature sensor inside the deck, it will warn you if the controller or the battery are too hot.
14 | General | 2 | uint8_t | Humidity_warning |  |  | 20 | 100 | 80 | 10 |  | Humidity warning | RH |  | seek_bar | 1 | Humidity warning | 10 | 5 | RH | Trig an error indicator on the display or the smartphone application if this humidy threshold is reached. If you place the humidity sensor inside the deck, it will warn you if the water is entered inside the deck.
47 | General | 2 | uint8_t | Auto_power_off | ^sd_.* | None 2 min 3 min 4 min 5 min 10 min 15 min 20 min 30 min 60 min | 0 | 9 | 0 |  |  | Automatic power off |  |  | list | 1 | Auto power off | 1 | 1 |  | Automatically shutdown the escooter after this period when escooter is not moving.
15 | Smartphone display | 4 | int8_t | Smartdisplay_speed_adjustment |  |  | -100 | 100 | 0 |  | ^[-]?[0-9]+$ | Speed adjustment (in percent) |  | write -10 to decrease speed by 10% | edit_text_number_integer_signed | 0 | Speed adjustment |  |  |  | Use this value to correct the speed on the smartphone display. You can increase or decrease the speed.
16 | Smartphone display | 4 | uint8_t | Aux_relay_name |  | AUX DUAL LIGHT HORN RELAY | 0 | 4 | 0 |  |  | Aux relay name |  |  | list | 0 | Aux relay name |  |  |  | Change the name of the auxilary relay on the display and smartphone for the integrated relay action. Exemple : if you connect a light, you can display "light" on the dashboard instead of "aux".
17 | Smartphone display | 4 | uint8_t | Display_gps_speed_instead_of_escooter_speed |  |  | 0 | 1 | 0 |  |  | Display GPS speed instead of escooter speed |  |  | checkbox | 0 | Display GPS speed |  |  |  | Display GPS speed instead of escooter speed on the smartphone display.
18 | SmartDisplay | 5 | uint8_t | Default_mode_at_startup | ^sd_.* |  | 1 | 3 | 3 | 1 |  | Default mode at startup |  |  | seek_bar | 1 | Startup mode | 1 | 1 |  | Default speed mode after escooter power up.
19 | SmartDisplay | 5 | uint8_t | Default_eco_mode_at_startup | ^sd_.* | Max Medium None | 0 | 2 | 2 |  |  | Default eco mode at startup |  |  | list | 1 | Startup eco mode | 1 | 1 |  | Default eco mode after escooter power up.
20 | SmartDisplay | 5 | uint8_t | Default_acceleration | ^sd_.* | Maximum Very fast Fast Medium Slow Very slow | 0 | 5 | 0 |  |  | Default acceleration |  |  | list | 1 | Startup acceleration | 1 | 1 |  | Default acceleration mode after escooter power up.
21 | SmartDisplay | 5 | uint8_t | Default_electric_brake_at_startup | ^sd_.* |  | 0 | 5 | 3 | 1 |  | Default electric brake at startup |  |  | seek_bar | 1 | Startup ebrake | 1 | 1 |  | Default electric brake power mode after escooter power up.
22 | SmartDisplay | 5 | uint8_t | Pas_enabled | ^sd_.* |  | 0 | 1 | 0 |  |  | PAS enabled |  |  | checkbox | 1 | PAS enabled |  |  |  | The 'pedal assitance switch' will force you to push the escooter to start the engine. If you don't push the scooter, the throttle is not effective. The motor will engage as soon as 1km/h is reached.
23 | SmartDisplay | 5 | uint8_t | Abs_enabled | ^sd_.* |  | 0 | 1 | 0 |  |  | ABS enabled |  |  | checkbox | 1 | ABS enabled |  |  |  | Enable the anti-lock electric braking system (not advised, not well implemented on most escooters),
24 | SmartDisplay | 5 | uint8_t | Display_brightness | ^sd_.* |  | 50 | 100 | 100 | 10 |  | Display brightness |  |  | seek_bar | 1 | Display brightness | 10 | 5 |  | Set the SmartDisplay screen brightness.
25 | Electric brake | 6 | uint8_t | Ebrake_progressive_mode |  |  | 0 | 1 | 0 |  |  | Progressive mode |  |  | checkbox | 1 | Progressive mode |  |  |  | Enable the electric brake progressive mode.
26 | Electric brake | 6 | uint8_t | Ebrake_smart_brake_type |  | Controller Smart - Digital brake lever Smart - Analog brake lever Smart - Digital brake + throttle (exp) | 0 | 3 | 0 |  |  | Smart brake type |  |  | list | 1 | Type |  |  |  | If you enable the electric progressive mode, the braking feedback must arrive to the SmartElec device. <b>There is mulitple possibilities to wire the brake on the SmartElec and you MUST select the brake type according to your wiring</b> : - Controller : no specific wiring required, the brake feedback will come from the controller. This is slower and will add a delay of 200/300ms between the brake pressure and the electric brake activation. The brake force will be determined by the brake lever pressure time. Longer you press, stronger the electric brake will become. - Smart - Digital brake lever : a standard on/off brake lever is wired directly to the SmartElec device. This wiring has a faster reaction. The brake force will be determined by the brake lever pressure time. Longer you press, stronger the electric brake will become. - Smart - Analog brake lever : an analog brake lever (xiaomi type or any hall sensor brake lever) is wired to directly to the SmartElec device. This wiring is the best. The brake force will be determined by the brake lever pressure force. - Smart - Digital brake + throttle (experimental) : a standard on/off brake lever is wired directly to the SmartElec device and the throttle pressure set the brake force. You will need time to use this mode when riding.
62 | Electric brake | 6 | uint32_t | Ebrake_input_min_voltage |  |  | 500 | 1500 | 650 | 50 |  | Input min voltage (in millivolts) | millivolts |  | seek_bar | 1 | Input min voltage | 100 | 50 | mV | Throttle input signal voltage when the throttle is released. Note : if the motor is spinning when the throttle is not pressed, try to decrease this value.
63 | Electric brake | 6 | uint32_t | Ebrake_input_max_voltage |  |  | 2500 | 5000 | 3950 | 50 |  | Input max voltage (in millivolts) | millivolts |  | seek_bar | 1 | Input max voltage | 100 | 50 | mV | Throttle input signal voltage when the throttle is fully pressed Note : if the motor is not reaching max speed when the throttle is pressed, try to increase this value.
27 | Electric brake | 6 | uint8_t | Ebrake_min_power_value |  |  | 0 | 5 | 1 | 1 |  | Min power value |  |  | seek_bar | 1 | Min value | 1 | 1 |  | Define the minimum electric brake force when you start pressing the brake lever. Note : don't forget to calibrate the brake lever pressure for a better feeling.
28 | Electric brake | 6 | uint8_t | Ebrake_max_power_value |  |  | 0 | 5 | 5 | 1 |  | Max power value |  |  | seek_bar | 1 | Max value | 1 | 1 |  | Define the maximum electric brake force when you pressing the brake lever. Note : don't forget to calibrate the brake lever pressure for a better feeling.
29 | Electric brake | 6 | uint32_t | Ebrake_time_between_mode_shift |  |  | 100 | 2000 | 500 | 50 |  | Time between mode shift | milliseconds |  | seek_bar | 1 | Time between mode shift | 100 | 50 | ms | When using a digital brake lever (on/off switch on the lever), this period will determine when the brake force is increased to the next lever (from min to max) as long as you keep the brake active. Exemple : brake min = 1 / brake max = 3 / brake switch period = 500ms. When you start pressing the brake, it will set a electric brake force at 1. If you keep the brake pressed, 500ms later, it will set a electric brake force at 2, and 500ms later to 3. It will remain at 3 (max) until you release the brake lever.
30 | Electric brake | 6 | uint8_t | Ebrake_disabled_on_high_battery_voltage |  |  | 0 | 1 | 0 |  |  | Disabled on high battery voltage |  |  | checkbox | 1 | Disabled with bat, HV |  |  |  | Prevent power surge when braking if the battery is full or almost full. Electric brake generate current/voltage when used. If you use the electric brake when the battery is battery is full, the battery cannot take the energy and the controller will try to dissipate the energy... and can heat/blow. This option disable the electric brake until the baterry reach a threshold.
31 | Electric brake | 6 | uint8_t | Ebrake_disabled_percent_limit |  |  | 80 | 100 | 100 | 1 |  | Disabled percent limit | percent |  | seek_bar | 1 | Disabled with bat. HV | 5 | 1 | % | Battery load percent threshold to reach to enable electric brake.
32 | Throttle | 7 | uint8_t | Throttle_regeneration |  |  | 0 | 1 | 0 |  |  | Throttle regeneration |  |  | checkbox | 1 | Throttle regeneration |  |  |  | Enable throttle signal regeneration. This option allow you to modify the acceleration curve to make it more/less dynamic with different acceleration curves. <b>To enable this feature, you must wire the trottle jumpers according to the WIRING documentation.</b>
33 | Throttle | 7 | uint32_t | Throttle_input_min_voltage |  |  | 500 | 1500 | 650 | 50 |  | Input min voltage (in millivolts) | millivolts |  | seek_bar | 1 | Input min voltage | 100 | 50 | mV | Throttle input signal voltage when the throttle is released. Note : if the motor is spinning when the throttle is not pressed, try to decrease this value.
34 | Throttle | 7 | uint32_t | Throttle_input_max_voltage |  |  | 2500 | 5000 | 3950 | 50 |  | Input max voltage (in millivolts) | millivolts |  | seek_bar | 1 | Input max voltage | 100 | 50 | mV | Throttle input signal voltage when the throttle is fully pressed Note : if the motor is not reaching max speed when the throttle is pressed, try to increase this value.
35 | Throttle | 7 | uint32_t | Throttle_output_min_voltage |  |  | 500 | 2000 | 800 | 50 |  | Output min voltage (in millivolts) | millivolts |  | seek_bar | 1 | Output min voltage | 100 | 50 | mV | Throttle ouput signal voltage when the throttle is released. Note : if the motor is spinning when the throttle is not pressed, try to decrease this value.
36 | Throttle | 7 | uint32_t | Throttle_output_max_voltage |  |  | 2500 | 5000 | 3350 | 50 |  | Output max voltage (in millivolts) | millivolts |  | seek_bar | 1 | Output max voltage | 100 | 50 | mV | Throttle output signal voltage when the throttle is fully pressed Note : if the motor is not reaching max speed when the throttle is pressed, try to increase this value.
37 | Throttle | 7 | uint8_t | Throttle_output_curve |  | Linear Exponential 1 Exponential 2 Exponential 3 Exponential 4 Custom 6 points | 0 | 5 | 2 |  |  | Output curve |  |  | list | 1 | Output curve |  |  |  | This option modify the throttle response and acceleration curve. There is 3 main modes : - linear : same as original, except you can put an offset to increase the dead zone (with min input voltage) - exponential : those curves follow exponential functions, the acceleration becomes more violent as you reach the end the trigger pressure. Exponential 1 is soft but more violent than linear, Exponential 4 is very violent. - custom 6 points : 2 points are fixed (0% trigger pressure = 0% output / 100% trigger pressure = 100% output), with the next option, you can the set the output percent for 20, 40, 60 and 80% pressure on the trigger. It will interpolate the values between those pressure percentage to determine the ouput throttle percentage.
46 | Throttle | 7 | string | Throttle_output_curve_custom4 |  |  | 1 | 16 | 20,40,60,80 |  | ^[0-9]+(,[0-9]+){3}$ | Custom output curve points |  |  | edit_text_string | 0 | Custom output curve points |  |  |  | String of 4 values separated by commas. It will determine the output level for the 4 points (see custom curve option above) of 20, 40, 60, 80% pressure. Example with : 7, 15, 45, 75 ![](throttle_custom_curve.png)
38 | Escooter buttons | 8 | uint8_t | Button_1_short_press_action |  | None Speed limit ON/OFF Aux ON/OFF Mode switch 1/2/3 Mode switch 2/3 Eco switch NONE/MED/MAX Eco switch NONE/MED | 0 | 6 | 0 |  |  | Button 1 short press action |  |  | list | 1 | B1 short press |  |  |  | Set the button 1 short press action (for external buttons wired to the SmartElec) : - None : no action - Speed limitation ON/OFF : enable/disable the speed limiter - Aux ON/OFF : enable/disable the auxiliary relay output - Mode switch 1/2/3 : switch between speed modes - Mode switch 2/3 : switch between speed modes - Eco switch NONE/MED/MAX : switch between eco modes - Eco switch NONE/MED : switch between eco modes - Anti-theft manual lock ON : lock the escooter (motor power is locked, nobody can steal & ride with this mode) - Nitro boost continuous : switch speed mode to 3 while the button is pressed, then go back to original speed mode
39 | Escooter buttons | 8 | uint8_t | Button_1_long_press_action |  | None Speed limitation ON/OFF Aux ON/OFF Mode switch 1/2/3 Mode switch 2/3 Eco switch NONE/MED/MAX Eco switch NONE/MED Anti-theft manual lock ON Nitro boost continuous | 0 | 8 | 0 |  |  | Button 1 long press action |  |  | list | 1 | B1 long press |  |  |  | Set the button 1 long press action (for external buttons wired to the SmartElec) : - None : no action - Speed limitation ON/OFF : enable/disable the speed limiter - Aux ON/OFF : enable/disable the auxiliary relay output - Mode switch 1/2/3 : switch between speed modes - Mode switch 2/3 : switch between speed modes - Eco switch NONE/MED/MAX : switch between eco modes - Eco switch NONE/MED : switch between eco modes - Anti-theft manual lock ON : lock the escooter (motor power is locked, nobody can steal & ride with this mode) - Nitro boost continuous : switch speed mode to 3 while the button is pressed, then go back to original speed mode
40 | Escooter buttons | 8 | uint8_t | Button_2_short_press_action |  | None Speed limitation ON/OFF Aux ON/OFF Mode switch 1/2/3 Mode switch 2/3 Eco switch NONE/MED/MAX Eco switch NONE/MED | 0 | 6 | 0 |  |  | Button 2 short press action |  |  | list | 1 | B2 short press |  |  |  | Set the button 2 short press action (for external buttons wired to the SmartElec) : - None : no action - Speed limitation ON/OFF : enable/disable the speed limiter - Aux ON/OFF : enable/disable the auxiliary relay output - Mode switch 1/2/3 : switch between speed modes - Mode switch 2/3 : switch between speed modes - Eco switch NONE/MED/MAX : switch between eco modes - Eco switch NONE/MED : switch between eco modes - Anti-theft manual lock ON : lock the escooter (motor power is locked, nobody can steal & ride with this mode) - Nitro boost continuous : switch speed mode to 3 while the button is pressed, then go back to original speed mode Note : button 2 long press action allow you to enter the settings menu.
41 | Escooter buttons | 8 | uint8_t | Button_long_press_duration |  |  | 1 | 10 | 3 | 1 |  | Button long press duration | seconds |  | seek_bar | 1 | Button long press duration | 1 | 1 | s | If you press the button for this period, the SmartElec will launch the "long press" action.
42 | OTA update | 10 | string | Wifi_ssid |  |  | 1 | 32 |  |  | ^(.{0,32})$ | Wifi network name (SSID) |  |  | edit_text_string | 0 | Wifi network name |  |  |  | Wifi network SSID/name used for software updates.
43 | OTA update | 10 | string | Wifi_password |  |  | 1 | 32 |  |  | ^(.{0,32})$ | Wifi password |  |  | edit_text_password | 0 | Wifi password |  |  |  | Wifi network password used for software updates.
44 | SmartDisplay | 5 | uint8_t | Display_splash_screen | ^sd_.* |  | 0 | 1 | 1 | 1 |  | Display splash screen |  |  | checkbox | 1 | Display splash screen | 1 | 1 |  | Enable the splash screen at escotter startup
45 | SmartDisplay | 5 | uint8_t | Rotate_screen | ^sd_.* | Normal Inverted | 0 | 1 | 0 | 1 |  | Rotate screen |  |  | list | 1 | Rotate screen | 1 | 1 |  | Rotate screen if you mount the display in un unorthodox way.

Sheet: battery
 | 3 | 3.1 | 3.2 | 3.7 | 3.6 | full
1 | 3 | 3.1 | 3.2 | 3.7 | 3.6 | 4.2
2 | 6 | 6.2 | 6.4 | 7.4 | 7.2 | 8.4
3 | 9 | 9.3 | 9.6 | 11.1 | 10.8 | 12.6
4 | 12 | 12.4 | 12.8 | 14.8 | 14.4 | 16.8
5 | 15 | 15.5 | 16 | 18.5 | 18 | 21
6 | 18 | 18.6 | 19.2 | 22.2 | 21.6 | 25.2
7 | 21 | 21.7 | 22.4 | 25.9 | 25.2 | 29.4
8 | 24 | 24.8 | 25.6 | 29.6 | 28.8 | 33.6
9 | 27 | 27.9 | 28.8 | 33.3 | 32.4 | 37.8
10 | 30 | 31 | 32 | 37 | 36 | 42
11 | 33 | 34.1 | 35.2 | 40.7 | 39.6 | 46.2
12 | 36 | 37.2 | 38.4 | 44.4 | 43.2 | 50.4
13 | 39 | 40.3 | 41.6 | 48.1 | 46.8 | 54.6
14 | 42 | 43.4 | 44.8 | 51.8 | 50.4 | 58.8
15 | 45 | 46.5 | 48 | 55.5 | 54 | 63
16 | 48 | 49.6 | 51.2 | 59.2 | 57.6 | 67.2
17 | 51 | 52.7 | 54.4 | 62.9 | 61.2 | 71.4
18 | 54 | 55.8 | 57.6 | 66.6 | 64.8 | 75.6
19 | 57 | 58.9 | 60.8 | 70.3 | 68.4 | 79.8
20 | 60 | 62 | 64 | 74 | 72 | 84
21 | 63 | 65.1 | 67.2 | 77.7 | 75.6 | 88.2
22 | 66 | 68.2 | 70.4 | 81.4 | 79.2 | 92.4
23 | 69 | 71.3 | 73.6 | 85.1 | 82.8 | 96.6
24 | 72 | 74.4 | 76.8 | 88.8 | 86.4 | 100.8
25 | 75 | 77.5 | 80 | 92.5 | 90 | 105
26 | 78 | 80.6 | 83.2 | 96.2 | 93.6 | 109.2
27 | 81 | 83.7 | 86.4 | 99.9 | 97.2 | 113.4
28 | 84 | 86.8 | 89.6 | 103.6 | 100.8 | 117.6
29 | 87 | 89.9 | 92.8 | 107.3 | 104.4 | 121.8
30 | 90 | 93 | 96 | 111 | 108 | 126

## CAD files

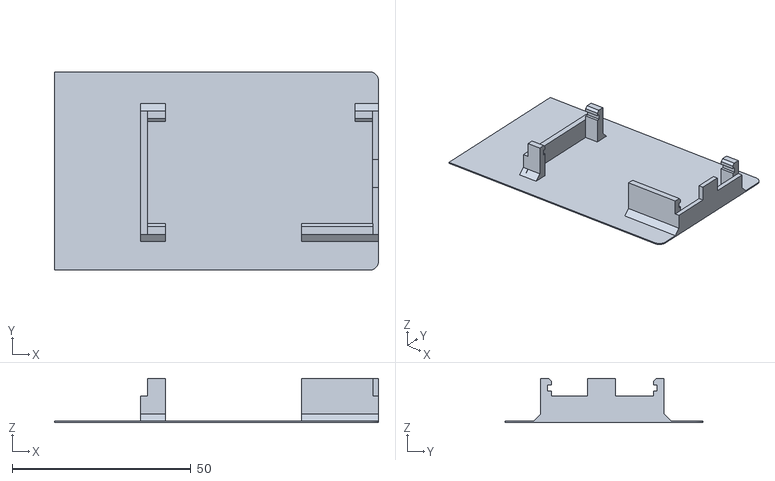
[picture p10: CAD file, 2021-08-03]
stl/Smart_Display_35_v2_separateur_clips.stl
90.6 x 55.5 x 12.4

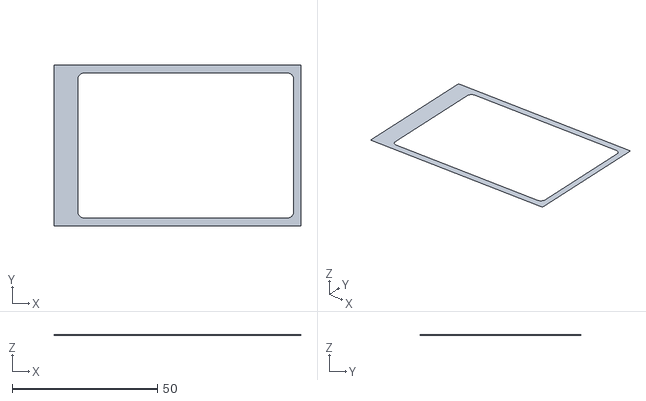
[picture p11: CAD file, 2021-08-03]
stl/Smart_Display_35_v2_cache.stl
85.0 x 55.5 x 0.2

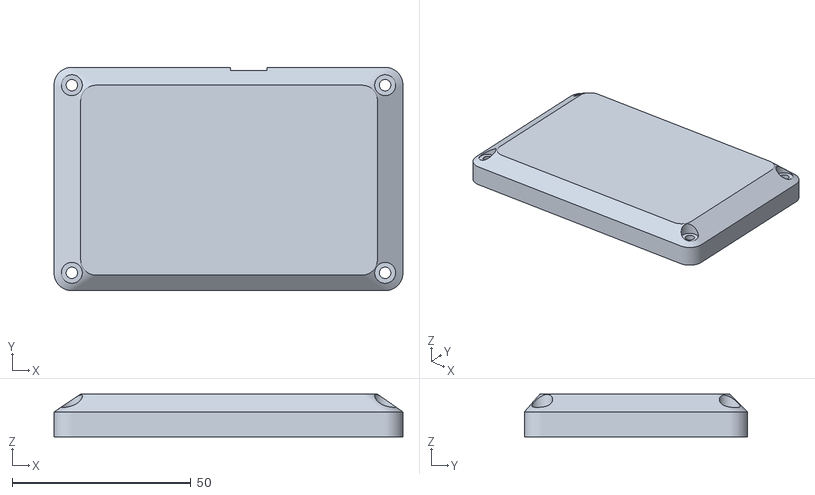
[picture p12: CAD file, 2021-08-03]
stl/Smart_Display_35_v2_couvercle_5mm_precut_v6.stl
97.6 x 62.5 x 12.0

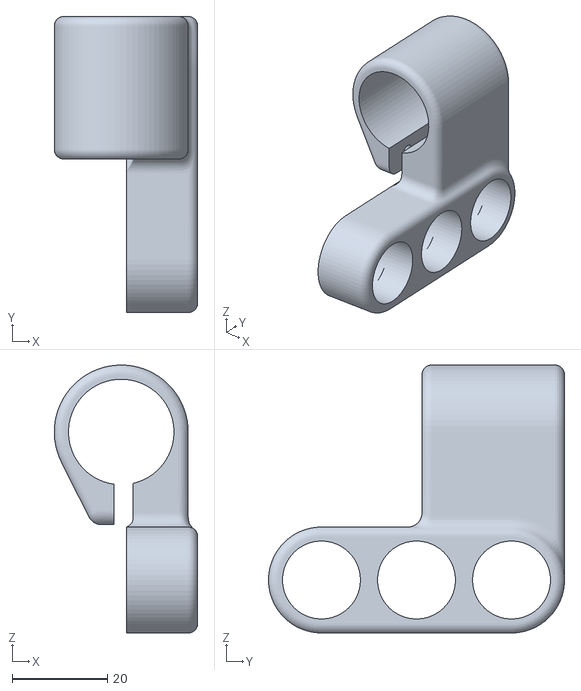
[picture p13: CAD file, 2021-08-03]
stl/Boitier_boutons.stl
30.2 x 62.3 x 56.4

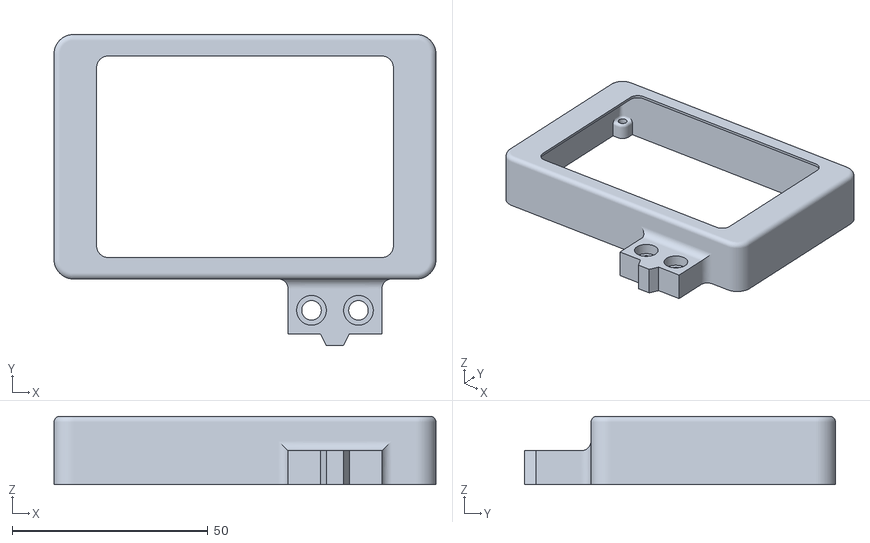
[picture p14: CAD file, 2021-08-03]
stl/Smart_Display_35_v2_boitier.stl
97.6 x 79.5 x 17.5

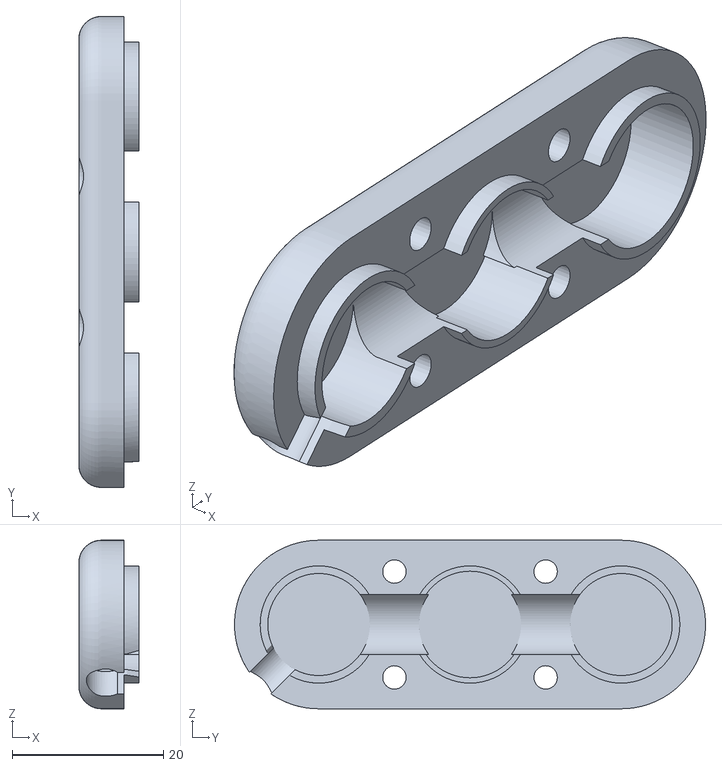
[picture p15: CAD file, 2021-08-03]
stl/Couvercle_Support_BTN _3 v1.stl
8.00 x 62.3 x 22.3

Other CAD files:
stl/Couvercle_Support_BTN _4 v1.stl

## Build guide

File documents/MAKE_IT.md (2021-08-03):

# How to make the your own ?

All electronic designs and software are open source. So, you can easily make your own board if you have some electronic skills.

## Produce the board with [JLCPBC](https://jlcpcb.com/)

The first step is : produce your board.
JLCPCB has interesting capacities : [PCB assembly](https://jlcpcb.com/smt-assembly).
They print your PCB and solder components on it.

It cost arround 40/50€ to produce the board.

The issue : they don't have all components.

You'll have to order the missing components on aliexpress or any electronic store and solder it yourself.

The major non included components are :
- SMD relays
- connectors
- Power supply capacitor
- Solid State Relay (DIP4 package)

Check the electronic project link on the [main github page](https://github.com/Koxx3/SmartController_SmartDisplay_ESP32#Schematics)

# After ordering the board PCB

Order the missing components !

Don't forget to order connectors :
- JST SM (2/3/6 pins)
- JST PH 2.0 (2/3/5/6 pins)

You can also add the external  :
- WCS1700 : current sensor
- Expansion boards (**PRO version** only)

# Ports usage and jumpers



:warning: Square in the connector mark the pin number 1. :warning:

## Ports

### [LC] For original controller display cable

Minimotors/Zero/Vsett wiring :
- 1 - serial / ESP to LCD
- 2 - serial / LCD to ESP
- 3 - throttle signal
- 4 - GND
- 5 - battery feedback
- 6 - battery power

VESC wiring : not connected

### [CT] For controller cable

Minimotors/Zero/Vsett wiring :
- 1 - serial / controller to ESP
- 2 - serial / ESP to controller
- 3 - throttle signal
- 4 - GND
- 5 - battery feedback
- 6 - battery power

VESC wiring :
- 1 - RX ESP / TX VESC
- 2 - TX ESP / RX VESC
- 3 - throttle
- 4 - GND
- 5 - not connected
- 6 - not connected

### [BKO] Brake output

Wiring :
- no pin order (relay)
- max voltage/current : depends of Solid state relay you placed

### [REL] Relay output

Wiring :
- no pin order (relay)
- max voltage/current : depends of Solid state relay you placed

### [BKI] Brake input

Analog brake wiring :
- 1 - signal
- 2 - GND
- 3 - 5V

Digital brake wiring :
- 1 - brake switch
- 2 - not connected
- 3 - brake switch

### [WCS] WCS1700 current sensor

Wiring:
- 1 - signal
- 2 - GND
- 3 - 5V

### [LCD] LCD display

Wiring :
- 1 - GND
- 2 - 3.3V
- 3 - SPI CLK
- 4 - SPI MOSI
- 5 - SPI RESET
- 6 - SPI DC
- 7 - Backlight control 3.3V
- 8 - Backlight control 5V

### [THR] Throttle signals

Wiring :
- 1 - signal
- 2 - GND
- 3 - 5V

### [BTN] Buttons & LEDs

Wiring :
- 1 - button 1
- 2 - button 2
- 3 - buttons LEDs
- 4 - button power
- 5 - GND

### [PWR] 5V output

Wiring :
- 1 - GND
- 2 - 5V

### [DHT/OW] Expansion board connector

Reserved for PRO version.

## Jumpers and other selections

### [JTH] Throttle signal
If you want to use the throttle curve modification of the Smart, solder 1&2 and 3&4 on the SMD jumper (don't bridge 2&3).

If you don't want to modify the throttle signal, solder 2&3 on the SMD jumper.

:warning: **The throttle signal modification by the Smart boards is dangerous because if the software crash, the escooter motor can continue to accelerate even if the throttle is released. Multiple protections have been added, but the risk still exists. Use it at your own risks !** :warning:

### [JPWR] Power switch & source
For SmartDisplay, you have a power latch. It allows to power the board and the escooter from the power button (see "Buttons" connector).

If you want to use the latch, close 1&2 on the SMD jumper.

If your controller needs a power feedback, solder 1&2&3.

For SmartController, you don't need to sodler anything.

### [X] VESC UART in 3.3V
- remove R20, R10, R3
- v1.6.2 : solder X jumper
- v1.4.2 : remove Q5 and solder collector pin to emitter pin.

# Wrap it
## SmartController
You need a wrap for 10.5cm / diameter 33mm
[Link](https://fr.aliexpress.com/item/4000787511699.html)

## SmartDisplay
Use the 3D prints available [here](/stl/)

# Once you assembled the board and the components 

Upload the applications :D

[Next steps ...](RUN.md)

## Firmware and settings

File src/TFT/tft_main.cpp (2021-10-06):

#include <SPI.h>

#include "SPIFFS.h"
#include "TFT/AnimatedGIF/AnimatedGIF.h"

#include "tft_main.h"
#include "tft_colors.h"

#include "Settings.h"
#include "SharedData.h"
#include "pinout.h"
#include "WiFi.h"

#include "TFT/fonts/FORCED_SQUARE10pt7b.h"
#include "TFT/fonts/FORCED_SQUARE12pt7b.h"
#include "TFT/fonts/FORCED_SQUARE14pt7b.h"
#include "TFT/fonts/FORCED_SQUARE18pt7b.h"
#include "TFT/fonts/FORCED_SQUARE6pt7b.h"
#include "TFT/fonts/FORCED_SQUARE7pt7b.h"
#include "TFT/fonts/FORCED_SQUARE8pt7b.h"
#include "TFT/fonts/FORCED_SQUARE9pt7b.h"

// Stock font and GFXFF reference handle
#define GFXFF 1

// Easily remembered name for the font
#define FONT_FORCED_SQUARE6pt7b &FORCED_SQUARE6pt7b
#define FONT_FORCED_SQUARE7pt7b &FORCED_SQUARE7pt7b
#define FONT_FORCED_SQUARE8pt7b &FORCED_SQUARE8pt7b
#define FONT_FORCED_SQUARE9pt7b &FORCED_SQUARE9pt7b
#define FONT_FORCED_SQUARE10pt7b &FORCED_SQUARE10pt7b
#define FONT_FORCED_SQUARE12pt7b &FORCED_SQUARE12pt7b
#define FONT_FORCED_SQUARE14pt7b &FORCED_SQUARE14pt7b
#define FONT_FORCED_SQUARE18pt7b &FORCED_SQUARE18pt7b

#if ((TFT_MODEL == 2) || (TFT_MODEL == 3)) // 3.5"
#define FONT_RED_LABEL FONT_FORCED_SQUARE10pt7b
#define FONT_UNIT FONT_FORCED_SQUARE10pt7b
#define FONT_UNIT_SMALL FONT_FORCED_SQUARE10pt7b
#define FONT_UNIT_HEIGH 10
#define FONT_NUMBER FONT_FORCED_SQUARE18pt7b
#define FONT_NUMBER_HEIGHT 18
#else
#define FONT_RED_LABEL FONT_FORCED_SQUARE6pt7b
#define FONT_UNIT FONT_FORCED_SQUARE7pt7b
#define FONT_UNIT_SMALL FONT_FORCED_SQUARE6pt7b
#define FONT_UNIT_HEIGH 7
#define FONT_NUMBER FONT_FORCED_SQUARE14pt7b
#define FONT_NUMBER_HEIGHT 14
#endif

#define SEP_LINE 2 * SCALE_FACTOR_X
#define UNIT_LEFT_MARGIN 5 * SCALE_FACTOR_X

#define SMALLEST_FONT_SIZE 4 * SCALE_FACTOR_Y
#define SMALL_FONT_SIZE 5 * SCALE_FACTOR_Y
#define MEDIUM_FONT_SIZE 8 * SCALE_FACTOR_Y
#define BIG_FONT_SIZE 18 * SCALE_FACTOR_Y

#if (TFT_MODEL == 1) // 2.4"
#define LINE_1Y 9 * SCALE_FACTOR_Y
#define LINE_2Y 23 * SCALE_FACTOR_Y
#define LINE_2Y_UNIT LINE_2Y + (27 * SCALE_FACTOR_Y)
#define LINE_3Y 79 * SCALE_FACTOR_Y
#define LINE_3Y_UNIT1 LINE_3Y + (94 * SCALE_FACTOR_Y) // Km/m speed
#define LINE_3Y_UNIT2 LINE_3Y + (26 * SCALE_FACTOR_Y) // speed max
#define LINE_3Y_UNIT3 LINE_3Y + (15 * SCALE_FACTOR_Y) // Km/h speed max
#define LINE_4Y 210 * SCALE_FACTOR_Y
#define LINE_4Y_UNIT LINE_4Y + (22 * SCALE_FACTOR_Y)
#define NB_BATTERY_BARS 17
#else // 3.5"
#define LINE_1Y 9 * SCALE_FACTOR_Y
#define LINE_2Y 23 * SCALE_FACTOR_Y
#define LINE_2Y_UNIT LINE_2Y + (25 * SCALE_FACTOR_Y)
#define LINE_3Y 79 * SCALE_FACTOR_Y
#define LINE_3Y_UNIT1 LINE_3Y + (92 * SCALE_FACTOR_Y) // Km/m speed
#define LINE_3Y_UNIT2 LINE_3Y + (25 * SCALE_FACTOR_Y) // speed max
#define LINE_3Y_UNIT3 LINE_3Y + (14 * SCALE_FACTOR_Y) // Km/h speed max
#define LINE_4Y 210 * SCALE_FACTOR_Y
#define LINE_4Y_UNIT LINE_4Y + (21 * SCALE_FACTOR_Y)
#define NB_BATTERY_BARS 17
#endif

// separation lines
// for left indicators
#define LINE_POINT1X 38 * SCALE_FACTOR_X
#define LINE_POINT1Y 58 * SCALE_FACTOR_Y
#define LINE_POINT2X (38 + 15) * SCALE_FACTOR_X
#define LINE_POINT2Y (58 + 15) * SCALE_FACTOR_Y
#define LINE_POINT3X (38 + 15) * SCALE_FACTOR_X
#define LINE_POINT3Y 173 * SCALE_FACTOR_Y
#define LINE_POINT4X 38 * SCALE_FACTOR_X
#define LINE_POINT4Y (173 + 15) * SCALE_FACTOR_Y
// upper
#define LINE_POINT5X 70 * SCALE_FACTOR_X
#define LINE_POINT5Y LINE_POINT1Y
// lower
#define LINE_POINT6X 70 * SCALE_FACTOR_X
#define LINE_POINT6Y LINE_POINT4Y

#define SPACE_INDICATORS_Y 16

#define COLUMN0 24 * SCALE_FACTOR_X
#define COLUMN1 39 * SCALE_FACTOR_X
#define COLUMN2 82 * SCALE_FACTOR_X
#define COLUMN3 118 * SCALE_FACTOR_X
#define COLUMN4 219 * SCALE_FACTOR_X
#define COLUMN5 225 * SCALE_FACTOR_X
#define COLUMN6 215 * SCALE_FACTOR_X
#define COLUMN7 247 * SCALE_FACTOR_X
#define COLUMN8 280 * SCALE_FACTOR_X //279
#define COLUMN9 292 * SCALE_FACTOR_X

#define SPEED_LIMITER_INDICATOR_WIDTH (7 * SCALE_FACTOR_X)
#define SPEED_LIMITER_INDICATOR_HEIGHT (8 * SCALE_FACTOR_Y)
#define LINE_TEXT_OFFSET 6

#define NORMAL_SPEED // Comment out for rame rate for render speed test

#define NB_LOOP_ANIM_GIF 1
#define GIF_PATH_SPLASH "/gifs/splash.gif"
#define GIF_PATH_OTA "/gifs/update.gif"

// Use hardware SPI (on Uno, #13, #12, #11) and the above for CS/DC
TFT_eSPI tft = TFT_eSPI();

// TODO : clean this...
extern SharedData shrd;
extern Settings settings;

const char *txt_temp = "TMP";
const char *txt_pas = "PAS";
const char *txt_volts = "VOLTS";
const char *txt_err = "ERR";
const char *txt_lck = "LCK";
const char *txt_auton = "AUTON";
const char *txt_r_time = "TIME";
const char *txt_trip = "TRIP";
const char *txt_hr = "HR";
const char *txt_power = "POWER";
const char *txt_brk = "BRK";
const char *txt_aux = "AUX";
const char *txt_kmh = "Km/h";
const char *txt_km = "Km";
const char *txt_max = "Max";
const char *txt_w = "W ";
const char *txt_v = "V";
const char *txt_c = "C";
const char *txt_space = " ";
const char *txt_m = "M";
const char *txt_h = "H";

static uint8_t oldShrdPasEnabled = 255;
static uint8_t oldShrdBrakePressedStatus = 255;
static uint8_t oldShrdCurrentTemperature = 255;
static uint8_t oldShrdCurrentHumidity = 255;
static uint8_t oldError = 255;
static uint8_t oldShrdIsLocked = 255;
static uint8_t oldAuxOrder = 255;

static uint8_t old_substate_case3 = 0;
static uint8_t old_substate_case7 = 0;
static uint8_t old_substate_case6 = 0;
static uint8_t old_substate_ota = 0;

bool lock = false;

//-------------------------------------------------------
//
// GIF fonctions
//
//-------------------------------------------------------
#define DISPLAY_WIDTH tft.width()

// rule: loop GIF at least during 3s, maximum 5 times, and don't loop/animate longer than 30s per GIF
const int maxLoopIterations = 5;   // stop after this amount of loops
const int maxLoopsDuration = 5000; // ms, max cumulated time after the GIF will break loop
const int maxGifDuration = 30000;  // ms, max GIF duration

// used to center image based on GIF dimensions
static int xOffset = 0;
static int yOffset = 0;

static int currentFile = 0;
static int lastFile = -1;

static File FSGifFile; // temp gif file holder

static void *GIFOpenFile(const char *fname, int32_t *pSize)
{
  //log_d("GIFOpenFile( %s )\n", fname );
  FSGifFile = SPIFFS.open(fname);
  if (FSGifFile)
  {
    *pSize = FSGifFile.size();
    return (void *)&FSGifFile;
  }
  return NULL;
}

static void GIFCloseFile(void *pHandle)
{
  File *f = static_cast<File *>(pHandle);
  if (f != NULL)
    f->close();
}

static int32_t GIFReadFile(GIFFILE *pFile, uint8_t *pBuf, int32_t iLen)
{
  int32_t iBytesRead;
  iBytesRead = iLen;
  File *f = static_cast<File *>(pFile->fHandle);
  // Note: If you read a file all the way to the last byte, seek() stops working
  if ((pFile->iSize - pFile->iPos) < iLen)
    iBytesRead = pFile->iSize - pFile->iPos - 1; // <-- ugly work-around
  if (iBytesRead <= 0)
    return 0;
  iBytesRead = (int32_t)f->read(pBuf, iBytesRead);
  pFile->iPos = f->position();
  return iBytesRead;
}

static int32_t GIFSeekFile(GIFFILE *pFile, int32_t iPosition)
{
  int i = micros();
  File *f = static_cast<File *>(pFile->fHandle);
  f->seek(iPosition);
  pFile->iPos = (int32_t)f->position();
  i = micros() - i;
  //log_d("Seek time = %d us\n", i);
  return pFile->iPos;
}

static void TFTDraw(int x, int y, int w, int h, uint16_t *lBuf)
{
  tft.pushRect(x + xOffset, y + yOffset, w, h, lBuf);
}

// Draw a line of image directly on the LCD
void GIFDraw(GIFDRAW *pDraw)
{
  uint8_t *s;
  uint16_t *d, *usPalette, usTemp[320];
  int x, y, iWidth;

  iWidth = pDraw->iWidth;
  if (iWidth > DISPLAY_WIDTH)
    iWidth = DISPLAY_WIDTH;
  usPalette = pDraw->pPalette;
  y = pDraw->iY + pDraw->y; // current line

  s = pDraw->pPixels;
  if (pDraw->ucDisposalMethod == 2)
  { // restore to background color
    for (x = 0; x < iWidth; x++)
    {
      if (s[x] == pDraw->ucTransparent)
        s[x] = pDraw->ucBackground;
    }
    pDraw->ucHasTransparency = 0;
  }
  // Apply the new pixels to the main image
  if (pDraw->ucHasTransparency)
  { // if transparency used
    uint8_t *pEnd, c, ucTransparent = pDraw->ucTransparent;
    int x, iCount;
    pEnd = s + iWidth;
    x = 0;
    iCount = 0; // count non-transparent pixels
    while (x < iWidth)
    {
      c = ucTransparent - 1;
      d = usTemp;
      while (c != ucTransparent && s < pEnd)
      {
        c = *s++;
        if (c == ucTransparent)
        {      // done, stop
          s--; // back up to treat it like transparent
        }
        else
        { // opaque
          *d++ = usPalette[c];
          iCount++;
        }
      } // while looking for opaque pixels
      if (iCount)
      { // any opaque pixels?
        TFTDraw(pDraw->iX + x, y, iCount, 1, (uint16_t *)usTemp);
        x += iCount;
        iCount = 0;
      }
      // no, look for a run of transparent pixels
      c = ucTransparent;
      while (c == ucTransparent && s < pEnd)
      {
        c = *s++;
        if (c == ucTransparent)
          iCount++;
        else
          s--;
      }
      if (iCount)
      {
        x += iCount; // skip these
        iCount = 0;
      }
    }
  }
  else
  {
    s = pDraw->pPixels;
    // Translate the 8-bit pixels through the RGB565 palette (already byte reversed)
    for (x = 0; x < iWidth; x++)
      usTemp[x] = usPalette[*s++];
    TFTDraw(pDraw->iX, y, iWidth, 1, (uint16_t *)usTemp);
  }
} /* GIFDraw() */

int gifPlay(AnimatedGIF *gif, char *gifPath, int16_t y_offset)
{ // 0=infinite

  gif->begin(BIG_ENDIAN_PIXELS);

  if (!gif->open(gifPath, GIFOpenFile, GIFCloseFile, GIFReadFile, GIFSeekFile, GIFDraw))
  {
    Serial.printf("Could not open gif %s", gifPath);
    return maxLoopsDuration;
  }

  int frameDelay = 0; // store delay for the last frame
  int then = 0;       // store overall delay

  // center the GIF !!
  int w = gif->getCanvasWidth();
  int h = gif->getCanvasHeight();
  xOffset = (tft.width() - w) / 2;
  yOffset = ((tft.height() - h) / 2) + y_offset;

  if (lastFile != currentFile)
  {
    Serial.printf("Playing %s [%d,%d] with offset [%d,%d]", gifPath, w, h, xOffset, yOffset);
    lastFile = currentFile;
  }

  while (gif->playFrame(true, &frameDelay))
  {
    then += frameDelay;
    if (then > maxGifDuration)
    { // avoid being trapped in infinite GIF's
      //log_w("Broke the GIF loop, max duration exceeded");
      break;
    }
  }

  gif->close();

  return then;
}

//-------------------------------------------------------
//
// Bakclight fonctions
//
//-------------------------------------------------------

void tftSetupBacklight()
{

  pinMode(PIN_SPI_BKL, OUTPUT);
  digitalWrite(PIN_SPI_BKL, 1);
  ledcSetup(0, 200, 10);
  ledcAttachPin(PIN_SPI_BKL, 0);
  ledcWrite(0, 0);
}

void tftBacklightFull()
{
  if (!lock)
  {
    uint16_t brigtness = map(settings.get_Display_brightness(), 0, 100, 0, 1023);
    ledcWrite(0, brigtness);
  }
}

void tftBacklightLow(bool lock_p)
{
  lock = lock_p;
  ledcWrite(0, 0);
}

//-------------------------------------------------------
//
// Main fonctions
//
//-------------------------------------------------------
void tftSetup(SharedData *shrd_p, Settings *settings_p)
{

  //shrd = shrd_p;
  //settings = settings_p;

  // dim screen for init
  tftBacklightLow(false);

  if (!SPIFFS.begin())
  {
    Serial.println("SPIFFS not found !!!");
  }

  tft.begin();
  tft.fillScreen(TFT_BLACK);
}

static char *Dfmt2_1(double v)
{
  static char x[40];

  /**** This does all the convertion and formatting you need ****/
  sprintf(x, "%02d.%01d", (int)v, (int)(10 * (v - (int)v)));
  return (x);
}

String timeToString()
{
  char str[10];
  unsigned long currentMillis = millis();
  int seconds = currentMillis / 1000;
  int minutes = seconds / 60;
  int hours = minutes / 60;
  seconds %= 60;
  minutes %= 60;
  hours %= 24;
  sprintf(str, "%01d:%02d:%02d", hours, minutes, seconds);
  return String(str);
}

void tftUpdateData(uint32_t i_loop)
{
  char fmt[10];

  if (i_loop == -2) // -2 / show splash screen
  {
    Serial.print("step -2");

    // init TFT
    tft.begin();
    tft.invertDisplay(1);
    if (settings.get_Rotate_screen() == settings.LIST_Rotate_screen_Normal) 
      tft.setRotation(3);
    else
      tft.setRotation(1);

    tft.fillScreen(TFT_BLACK);

    // Only if splash is enabled ...
    if (settings.get_Display_splash_screen() == 1)
    {
      // Initialise SPIFFS
      bool spiffs = SPIFFS.begin();
      if (!spiffs)
      {
        Serial.println("SPIFFS initialisation failed!");
      }
      else
      {

        // Display GIF image
        int loops = maxLoopIterations;          // max loops
        int durationControl = maxLoopsDuration; // force break loop after xxx ms
        AnimatedGIF gif;
        while (loops-- > 0 && durationControl > 0)
        {
          durationControl -= gifPlay(&gif, (char *)GIF_PATH_SPLASH, 0);
          gif.reset();
        }

        tftBacklightFull();

        // Show loading progress
        for (int i = 0; i < 10; i++)
        {
          tft.fillRect(i * (TFT_HEIGHT / 10), 0, (TFT_HEIGHT / 10) - 5, 6 * SCALE_FACTOR_Y, MY_TFT_WHITE);
          delay(250);
        }
      }
    }
    else
    {
      tftBacklightFull();
    }
  }
  else if (i_loop == -1) // init fix datas after
  {

    // reset indicators status
    oldShrdPasEnabled = 255;
    oldShrdBrakePressedStatus = 255;
    oldShrdCurrentTemperature = 255;
    oldShrdCurrentHumidity = 255;
    oldError = 255;
    oldShrdIsLocked = 255;
    oldAuxOrder = 255;

    tft.fillScreen(TFT_BLACK);

    // init TFT settings
    tft.setTextSize(1);

    tft.setFreeFont(FONT_RED_LABEL);
    // draw interface - labels
    tft.setTextColor(TFT_RED, TFT_BLACK);
    tft.setTextDatum(BR_DATUM);
    tft.drawString(txt_volts, COLUMN4, LINE_2Y - LINE_TEXT_OFFSET, GFXFF);
    tft.drawString(txt_auton, COLUMN3, LINE_2Y - LINE_TEXT_OFFSET, GFXFF);
    tft.drawString(txt_r_time, COLUMN6, LINE_4Y - LINE_TEXT_OFFSET, GFXFF);
    tft.drawString(txt_trip, COLUMN9, LINE_4Y - LINE_TEXT_OFFSET, GFXFF);
    if (shrd.owb_ds9990_present || shrd.shtc3_present || shrd.currentSensorPresent > 0)
      tft.drawString(txt_power, COLUMN2, LINE_4Y - LINE_TEXT_OFFSET, GFXFF);

    // draw interface - units
    tft.setFreeFont(FONT_UNIT);
    tft.setTextColor(MY_TFT_WHITE, TFT_BLACK);
    tft.setTextDatum(BL_DATUM);
    // autonomy "kms"
    tft.drawString(txt_km, COLUMN3 + UNIT_LEFT_MARGIN, LINE_2Y_UNIT, GFXFF);
    // voltage "volts"
    tft.drawString(txt_v, COLUMN4 + UNIT_LEFT_MARGIN, LINE_2Y_UNIT, GFXFF);

    // power "watts"
    if (shrd.owb_ds9990_present || shrd.shtc3_present || shrd.currentSensorPresent > 0)
      tft.drawString(txt_w, COLUMN2 + UNIT_LEFT_MARGIN, LINE_4Y_UNIT, GFXFF);

    // trip "km/h"
    tft.drawString(txt_km, COLUMN9 + UNIT_LEFT_MARGIN, LINE_4Y_UNIT, GFXFF);

    // Max Speed : "Max" & "km/h"
    tft.setFreeFont(FONT_UNIT_SMALL);
    tft.drawString(txt_kmh, COLUMN8 + UNIT_LEFT_MARGIN, LINE_3Y_UNIT2, GFXFF);
    tft.drawString(txt_max, COLUMN8 + UNIT_LEFT_MARGIN, LINE_3Y_UNIT3, GFXFF);

    // Current speed : big "km/h"
    tft.setFreeFont(FONT_NUMBER);
    tft.drawString(txt_kmh, COLUMN5 + UNIT_LEFT_MARGIN, LINE_3Y_UNIT1, GFXFF);

    // draw grid
    tft.drawLine(0, LINE_POINT1Y, LINE_POINT1X, LINE_POINT1Y, MY_TFT_DARK_DIGIT_DISABLED);
    tft.drawLine(LINE_POINT1X, LINE_POINT1Y, LINE_POINT2X, LINE_POINT2Y, MY_TFT_DARK_DIGIT_DISABLED);
    tft.drawLine(LINE_POINT2X, LINE_POINT2Y, LINE_POINT3X, LINE_POINT3Y, MY_TFT_DARK_DIGIT_DISABLED);
    tft.drawLine(LINE_POINT3X, LINE_POINT3Y, LINE_POINT4X, LINE_POINT4Y, MY_TFT_DARK_DIGIT_DISABLED);
    tft.drawLine(LINE_POINT4X, LINE_POINT4Y, 0, LINE_POINT4Y, MY_TFT_DARK_DIGIT_DISABLED);

    tft.drawLine(LINE_POINT5X, LINE_POINT5Y, TFT_HEIGHT, LINE_POINT5Y, MY_TFT_DARK_DIGIT_DISABLED);
    tft.drawLine(LINE_POINT6X, LINE_POINT6Y, TFT_HEIGHT, LINE_POINT6Y, MY_TFT_DARK_DIGIT_DISABLED);
  }
  else if (shrd.inOtaMode) // OTA BLE/Wifi
  {

    if (old_substate_ota == 0)
    {
      // Clear screen
      tft.fillScreen(TFT_BLACK);

      old_substate_ota++;
    }
    else if (old_substate_ota == 1)
    {
      // Display GIF image
      int loops = maxLoopIterations;          // max loops
      int durationControl = maxLoopsDuration; // force break loop after xxx ms
      AnimatedGIF gif;
      while (loops-- > 0 && durationControl > 0)
      {
        durationControl -= gifPlay(&gif, (char *)GIF_PATH_OTA, -20);
        gif.reset();
      }

      old_substate_ota++;
    }
    else if (old_substate_ota == 2)
    {

      // Wait for wifi connection
      delay(500);

      // Display flashing informations
#if ((TFT_MODEL == 2) || (TFT_MODEL == 3)) // 3.5"
      tft.setFreeFont(FONT_FORCED_SQUARE12pt7b);
#else
      tft.setFreeFont(FONT_FORCED_SQUARE9pt7b);
#endif
      tft.setTextColor(MY_TFT_WHITE, TFT_BLACK);
      tft.setTextDatum(BC_DATUM);
      String str_ota_mode;
      if (shrd.inOtaMode == OTA_IDE)
      {
        str_ota_mode = "Mode : IDE server";
      }
      else
      {
        str_ota_mode = "Mode : Wifi server / Version : " + (String)shrd.inOtaModeVersion;
      }
      tft.drawString("Downloading and flashing", TFT_HEIGHT / 2, 190, GFXFF);
      tft.drawString(str_ota_mode, TFT_HEIGHT / 2, 210, GFXFF);

      String wifiStr = "";
      if (shrd.inOtaMode == OTA_IDE)
      {
        if (WiFi.localIP().toString() != "0.0.0.0")
        {
          wifiStr = "Wifi : " + settings.get_Wifi_ssid() + " / IP : " + WiFi.localIP().toString();
          tft.drawString(wifiStr, TFT_HEIGHT / 2, 230, GFXFF);

          old_substate_ota++;
        }
        else
        {
          wifiStr = "Wifi : " + settings.get_Wifi_ssid() + " / IP : waiting";
          tft.drawString(wifiStr, TFT_HEIGHT / 2, 230, GFXFF);

          // wait for wifi connection
          delay(500);
        }
      }
      else
      {
        wifiStr = "Wifi : " + settings.get_Wifi_ssid();
        tft.drawString(wifiStr, TFT_HEIGHT / 2, 230, GFXFF);
        old_substate_ota++;
      }
    }
  }
  else
  {
    switch (i_loop % 100)
    {
    case 0:
    {
      int speed = shrd.speedCurrent;
      if (speed > 199)
        speed = 199;
      if ((shrd.speedLimiter) && (speed > 25))
        speed = 25;

      sprintf(fmt, "%3d", (int)speed);
      tft_util_draw_number(&tft, fmt, COLUMN5, LINE_3Y, MY_TFT_WHITE, TFT_BLACK, 5, BIG_FONT_SIZE);

      break;
    }

    case 1:
    {
      int speed = shrd.speedMax;
      if (speed > 199)
        speed = 199;
      if ((shrd.speedLimiter) && (speed > 25))
        speed = 25;

      sprintf(fmt, "%3d", (int)speed);
      tft_util_draw_number(&tft, fmt, COLUMN8, LINE_3Y, MY_TFT_WHITE, TFT_BLACK, 5, SMALL_FONT_SIZE);
      break;
    }

    case 2:
    {
      // mode
      sprintf(fmt, "%01.0f", (float)shrd.modeOrder);
      tft_util_draw_number(&tft, fmt, COLUMN1, LINE_1Y, MY_TFT_WHITE, TFT_BLACK, 5, MEDIUM_FONT_SIZE);

      // eco mode
      String txt_eco;
      if (shrd.ecoOrder == 2)
        txt_eco = "   ";
      else if (shrd.ecoOrder == 1)
        txt_eco = "L";
      else if (shrd.ecoOrder == 0)
        txt_eco = "H";

      // Draw unit
      tft.setTextColor(MY_TFT_WHITE, TFT_BLACK);                                //UNIT
      tft.setTextDatum(BL_DATUM);                                               //UNIT
      tft.setFreeFont(FONT_UNIT);                                               //UNIT SIZE/FONT
      tft.drawString(txt_eco, COLUMN1 + UNIT_LEFT_MARGIN, LINE_2Y_UNIT, GFXFF); //DRAW UNIT ON DISPLAY

      // Switch font back
      tft.setFreeFont(FONT_NUMBER); //SET FONT FOR DATA

      break;
    }

    case 3:
    {
      float data;
      String txt_label;
      String txt_unit;
      bool shouldClear = false;

      if (shrd.owb_ds9990_present || shrd.shtc3_present || shrd.currentSensorPresent > 0)
      {
        if ((shrd.currentSensorPresent > 0) && (!(shrd.speedCurrent == 0 && shrd.brakePressedStatus == 1)))
        {
          // CASE POWER (With current sensor)
          txt_label = "  " + (String)txt_power;
          txt_unit = "W ";
          data = ((shrd.currentActual / 1000.0) * (shrd.voltageActual / 1000.0));
          data = constrain(data, 0, 65535);
          sprintf(fmt, "%05.0f", data);

          // check substate change
          if (old_substate_case3 == 1)
          {
            shouldClear = true;
          }
          old_substate_case3 = 0;
        }
        else
        {
          // CASE TEMP (Without current sensor, by default)
          txt_label = "       " + (String)txt_temp;
          txt_unit = "C ";
          sprintf(fmt, "%02.0f", shrd.currentTemperature);

          // check substate change
          if (old_substate_case3 == 0)
          {
            shouldClear = true;
          }
          old_substate_case3 = 1;
        }

        if (shouldClear)
        {
          // Clear number space
          tft.fillRect(0, LINE_4Y, COLUMN2, (SMALLEST_FONT_SIZE * 5), TFT_BLACK);

          // Draw label
          tft.setTextColor(TFT_RED, TFT_BLACK);                                  //LABEL
          tft.setTextDatum(BR_DATUM);                                            //LABEL
          tft.setFreeFont(FONT_RED_LABEL);                                       //LABEL SIZE/FONT
          tft.drawString(txt_label, COLUMN2, LINE_4Y - LINE_TEXT_OFFSET, GFXFF); //DRAW LABEL ON DISPLAY

          // Draw unit
          tft.setTextColor(MY_TFT_WHITE, TFT_BLACK);                                 //UNIT
          tft.setTextDatum(BL_DATUM);                                                //UNIT
          tft.setFreeFont(FONT_UNIT);                                                //UNIT SIZE/FONT
          tft.drawString(txt_unit, COLUMN2 + UNIT_LEFT_MARGIN, LINE_4Y_UNIT, GFXFF); //DRAW UNIT ON DISPLAY

          // Switch font back
          tft.setFreeFont(FONT_NUMBER); //SET FONT FOR DATA
        }
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

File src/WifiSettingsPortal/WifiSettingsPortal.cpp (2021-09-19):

#include <WiFi.h>
#include <WebServer.h>
#include <SPIFFS.h>
#include <AutoConnect.h>
#include "Settings.h"
#include <time.h>
#include "SharedData.h"
#include "BLE/BluetoothHandler.h"
#include "main.h"
#include <WebSocketsServer.h>
#include "ArduinoJson.h"

using WebServerClass = WebServer;

Settings *WifiSettingsPortal_settings;
SharedData *WifiSettingsPortal_shrd;
BluetoothHandler *WifiSettingsPortal_blh;

WebServerClass server;
WebSocketsServer webSocket = WebSocketsServer(81);
AutoConnect portal(server);
AutoConnectConfig config;

// General style elements
ACStyle(ACE_Style1, "label{display:inline-block;padding-right: 10px !important;padding-left: 0px !important;}");
ACStyle(ACE_Style2, "input[type='button']{background-color:#303F9F; border-color:#303F9F}");
ACStyle(ACE_Style3, "select{width:44%} h2{ color:#303F9F;padding:10px; }");
ACStyle(ACE_Style4, ".noorder{width:100%}.noorder label{display:inline-block;width:40%;cursor:pointer;padding:5px}.noorder .noorder input[type='text']{width:40%} .noorder input[type='password']{width:40%} .noorder input[type='text']{width:40%}");

// Settings page
ACSubmit(ACE_SETTINGS_Save, "Save", "/settingssave");
ACSubmit(ACE_SETTINGS_Discard, "Discard", "/settingspage");
ACElement(ACE_SETTINGS_Js1, "");
#include "WifiSettingsPortalSpecs.h"

// Settings sage
ACText(ACE_SETTINGS_SAVE_header, "<h4>Settings has been saved.</h4>", "text-align:center");
ACSubmit(ACE_SETTINGS_SAVE_confirm, "Ok", "/settingspage");
AutoConnectAux settingsSaveAux("/settingssave", "SmartElec settings", false, {ACE_Style2, ACE_Style3, ACE_Style4, ACE_SETTINGS_SAVE_header, ACE_SETTINGS_SAVE_confirm});

//format bytes
String formatBytes(size_t bytes)
{
  if (bytes < 1024)
  {
    return String(bytes) + "B";
  }
  else if (bytes < (1024 * 1024))
  {
    return String(bytes / 1024.0) + "KB";
  }
  else if (bytes < (1024 * 1024 * 1024))
  {
    return String(bytes / 1024.0 / 1024.0) + "MB";
  }
  else
  {
    return String(bytes / 1024.0 / 1024.0 / 1024.0) + "GB";
  }
}

String getContentType(String filename)
{
  if (server.hasArg("download"))
  {
    return "application/octet-stream";
  }
  else if (filename.endsWith(".htm"))
  {
    return "text/html";
  }
  else if (filename.endsWith(".html"))
  {
    return "text/html";
  }
  else if (filename.endsWith(".css"))
  {
    return "text/css";
  }
  else if (filename.endsWith(".js"))
  {
    return "application/javascript";
  }
  else if (filename.endsWith(".png"))
  {
    return "image/png";
  }
  else if (filename.endsWith(".gif"))
  {
    return "image/gif";
  }
  else if (filename.endsWith(".jpg"))
  {
    return "image/jpeg";
  }
  else if (filename.endsWith(".ico"))
  {
    return "image/x-icon";
  }
  else if (filename.endsWith(".xml"))
  {
    return "text/xml";
  }
  else if (filename.endsWith(".pdf"))
  {
    return "application/x-pdf";
  }
  else if (filename.endsWith(".zip"))
  {
    return "application/x-zip";
  }
  else if (filename.endsWith(".js.gz"))
  {
    return "application/javascript";
  }
  else if (filename.endsWith(".gz"))
  {
    return "application/x-gzip";
  }
  return "text/plain";
}

bool exists(String path)
{
  bool yes = false;
  File file = SPIFFS.open(path, "r");
  if (!file.isDirectory())
  {
    yes = true;
  }
  file.close();
  return yes;
}

bool handleFileRead(String path)
{
  Serial.println("handleFileRead: " + path);
  if (path.endsWith("/"))
  {
    path += "index.htm";
  }
  String contentType = getContentType(path);
  String pathWithGz = path + ".gz";
  if (exists(pathWithGz) || exists(path))
  {
    if (exists(pathWithGz))
    {
      path += ".gz";
    }
    File file = SPIFFS.open(path, "r");
    server.streamFile(file, contentType);
    file.close();
    return true;
  }
  return false;
}
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

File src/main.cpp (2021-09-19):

//////////////////////////////////////////
// TODO : VESC-EYE => error indicator on EYE
// TODO : auto mode shift on low battery
// TODO : reduce SHTC3 read time - brake read function in 2 parts
// TODO : VESC / configurable speed limits
//           - 20/25
//           - 35/30/35
//           - unlimited speed
// TODO : VESC / configure ECO & BOOST
//           - eco 0.6 multiplier for phase and 0.7 for battery current
//           - normal no change
//           - boost multiplier 1.2 for battery and phase currents
// TODO : VESC / TFT & app warning indicator boost
// TODO : VESC / limit boost with threshold if MOSFET are too high
// BUG : Minimo - original regulator perturbation
// BUG : current init = false max current/power on smartphone ??
//////////////////////////////////////////

//////------------------------------------
////// Inludes

#include "main.h"
#include "BLE/BluetoothHandler.h"
#include "Battery/Battery.h"
#include "Buttons/Buttons.h"
#include "DHT/dht_nonblocking.h"
#include "OTA/OTA_wifi.h"
#include "Settings.h"
#include "SharedData.h"
#include "TFT/tft_main.h"
#include "TFT/tft_settings_menu.h"
#include "debug.h"
#include "esp32-hal-uart.h"
#include "filters/MedianFilter.h"
#include "pinout.h"
#include "tools/utils.h"
#include "Settings.h"
#include "Settings2.h"
#include "WifiSettingsPortal/WifiSettingsPortal.h"
#include "Controllers/KellyUart.h"
#include "Controllers/MinimoUart.h"
#include "Controllers/SmartEsc.h"
#include "Controllers/VescUart.h"
#include "Controllers/ZeroUart.h"
#include "ioprocessing.h"
#include "OWB/owb_process.h"

//////------------------------------------
////// Defines

// SMART CONFIGURATION
#if BUILD_CONTROLLER_MINIMOTORS || BUILD_DISPLAY_EYE
MinimoUart minomoCntrl;
#endif
#if BUILD_CONTROLLER_VESC
VescUart vescCntrl;
#endif
#if BUILD_CONTROLLER_KELLY
KellyUart kellyCntrl;
#endif
#if BUILD_CONTROLLER_SMART_ESC
SmartEsc smartEscCntrl;
#endif
#if BUILD_CONTROLLER_ZERO
ZeroUart zeroCntrl;
#endif

// UART
#define BAUD_RATE_CONSOLE 921600

// distance
#define SPEED_TO_DISTANCE_CORRECTION_FACTOR 1

#define DEBUG_ESP_HTTP_UPDATE 1

#define ENABLE_TEMPERATURE_INT_READ 1
#define ENABLE_VOLTAGE_EXT_READ 1
#define ENABLE_BRAKE_ANALOG_EXT_READ 1
#define ENABLE_ONEWIRE 1
#define ENABLE_WIFI 1
#define ENABLE_WATCHDOG 1

#define WATCHDOG_TIMEOUT 1000 // 1s // time in ms to trigger the watchdog

#define USE_CURRENT_FROM_MINIMO_CONTROLLER 0

//////------------------------------------
////// Variables

// Tasks handlers
TaskHandle_t htaskUpdateTFT;
TaskHandle_t htaskProcessWifiBlocking;
TaskHandle_t htaskProcessButtons;
TaskHandle_t htaskProcessOwb;

// Time
unsigned long timeLoop = 0;
unsigned long timeLoopMax = 0;

// Watchdog
hw_timer_t *timer = NULL;

// Serial
float serialRcvValue = 0;

// Settings
int begin_soft = 0;
int begin_hard = 0;

char bleLog[50] = "";

HardwareSerial hwSerCntrl(1);
HardwareSerial hwSerLcd(2);

SharedData shrd;

int i_loop = 0;

Buttons btns;

Settings settings;
Settings2 settings2;
BluetoothHandler blh;

//////------------------------------------
//////------------------------------------
////// Setups

void setupPins()
{

  pinMode(PIN_IN_OUT_ONEWIRE, INPUT_PULLUP);
  pinMode(PIN_IN_BUTTON1, INPUT_PULLUP);
  pinMode(PIN_IN_BUTTON2, INPUT_PULLUP);
  pinMode(PIN_IN_VOLTAGE, INPUT);
  pinMode(PIN_IN_CURRENT, INPUT);
  pinMode(PIN_OUT_RELAY, OUTPUT);
  pinMode(PIN_OUT_BRAKE, OUTPUT);
  pinMode(PIN_OUT_LED_BUTTON1, OUTPUT);
  pinMode(PIN_IN_ABRAKE, INPUT);
  pinMode(PIN_IN_ATHROTTLE, INPUT);
#if (PCB >= 142)
  pinMode(PIN_OUT_POWER_LATCH, OUTPUT);
  pinMode(PIN_IN_BUTTON_PWR, INPUT);
#endif
}

void setupSerial()
{

#if BUILD_CONTROLLER_MINIMOTORS || BUILD_DISPLAY_EYE
  minomoCntrl.setSettings(&settings);
  minomoCntrl.setSharedData(&shrd);
  minomoCntrl.setBluetoothHandler(&blh);
#endif

#if BUILD_CONTROLLER_MINIMOTORS
  // minimotor controller
  hwSerCntrl.begin(MINIMO_BAUD_RATE, SERIAL_8N1, PIN_SERIAL_CNTRL_TO_ESP, PIN_SERIAL_ESP_TO_CNTRL);
  minomoCntrl.setControllerSerialPort(&hwSerCntrl);
  hwSerCntrl.setUartIrqIdleTrigger(0);
#endif

#if BUILD_DISPLAY_EYE
  // minimotor display
  hwSerLcd.begin(MINIMO_BAUD_RATE, SERIAL_8N1, PIN_SERIAL_LCD_TO_ESP, PIN_SERIAL_ESP_TO_LCD);
  minomoCntrl.setLcdSerialPort(&hwSerLcd);
  hwSerLcd.setUartIrqIdleTrigger(0);
#endif

#if BUILD_CONTROLLER_ZERO || BUILD_DISPLAY_QSS4
  zeroCntrl.setSettings(&settings);
  zeroCntrl.setSharedData(&shrd);
  zeroCntrl.setBluetoothHandler(&blh);
#endif

#if BUILD_CONTROLLER_ZERO
  // zero controller
  hwSerCntrl.begin(ZERO_BAUD_RATE, SERIAL_8N1, PIN_SERIAL_CNTRL_TO_ESP, PIN_SERIAL_ESP_TO_CNTRL);
  zeroCntrl.setControllerSerialPort(&hwSerCntrl);
  hwSerCntrl.setUartIrqIdleTrigger(0);
#endif

#if BUILD_DISPLAY_QSS4
  // zero display
  hwSerLcd.begin(ZERO_BAUD_RATE, SERIAL_8N1, PIN_SERIAL_LCD_TO_ESP, PIN_SERIAL_ESP_TO_LCD);
  zeroCntrl.setLcdSerialPort(&hwSerLcd);
  hwSerLcd.setUartIrqIdleTrigger(0);
#endif

#if BUILD_CONTROLLER_VESC
  hwSerCntrl.begin(BAUD_RATE_VESC, SERIAL_8N1, PIN_SERIAL_CNTRL_TO_ESP, PIN_SERIAL_ESP_TO_CNTRL);
  vescCntrl.setSerialPort(&hwSerCntrl);
  vescCntrl.setup(&shrd, &blh, &settings);

#if DEBUG_DISPLAY_VESC_FRAME
  vescCntrl.setDebugPort(&Serial);
#endif
#endif

#if BUILD_CONTROLLER_KELLY
  hwSerCntrl.begin(BAUD_RATE_KELLY, SERIAL_8N1, PIN_SERIAL_CNTRL_TO_ESP, PIN_SERIAL_ESP_TO_CNTRL);
  kellyCntrl.setSerialPort(&hwSerCntrl);
  kellyCntrl.setDebugPort(&Serial);
  hwSerCntrl.setUartIrqIdleTrigger(1);
#endif

}

void saveBleLockForced()
{
  settings2.saveBleLockForced();
}
void saveOdo()
{
  settings2.saveOdo();
}
void saveBatteryCalib()
{
  settings2.saveBatteryCalib();
}
void convertBrakePressure()
{
  
  // init brake pressures .... dirty patch
  shrd.brakeMinPressureRaw = (settings.get_Ebrake_input_min_voltage() / 1000.0 / ANALOG_TO_VOLTS_5V) + 200;
  shrd.brakeMaxPressureRaw = settings.get_Ebrake_input_max_voltage() / 1000.0 / ANALOG_TO_VOLTS_5V;
  Serial.println("        brakeMinPressureRaw = "  + (String)shrd.brakeMinPressureRaw);
  Serial.println("        brakeMaxPressureRaw = "  + (String)shrd.brakeMaxPressureRaw);
}
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

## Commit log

2021-07-29 fix analog current sensor read conditions
    [main.cpp]
2021-07-29 improve VESC lib
2021-08-03 add schematics
2021-09-16 fix VESC processing
2021-09-16 fix SHTC3 read if setup failed
    [ioprocessing.cpp]
2021-09-18 process & display I2C error
    [BluetoothHandler.cpp, SharedData.h, ioprocessing.cpp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]
2021-09-19 new settings
    [params.xls]
2021-09-19 new brake calibration from settings
2021-09-19 some fixes
    [params.xls]
2021-10-06 avoid crash if taimetable not present
    [tft_main.cpp]
